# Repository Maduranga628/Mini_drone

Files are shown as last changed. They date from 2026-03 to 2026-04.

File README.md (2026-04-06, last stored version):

## ESP-Drone

* [中文](./README_cn.md)

### Introduction

**ESP-Drone** is an open source solution based on Espressif ESP32/ESP32-S2/ESP32-S3 Wi-Fi chip, which can be controlled by a mobile APP or gamepad over **Wi-Fi** connection. ESP-Drone comes with **simple hardware**, **clear and extensible code architecture**, and therefore this project can be used in **STEAM education** and other fields. The main code is ported from **Crazyflie** open source project with **GPL3.0** protocol.

> Currently support ESP32、ESP32S2、ESP32S3, please using ESP-IDF [release/v4.4](https://docs.espressif.com/projects/esp-idf/en/release-v4.4/esp32s2/get-started/index.html) branch as your develop environment

ESP-Drone

For more information, please check the sections below:
* **Getting Started**: [Getting Started](https://docs.espressif.com/projects/espressif-esp-drone/zh_CN/latest/gettingstarted.html)
* **Hardware Schematic**：[Hardware](https://docs.espressif.com/projects/espressif-esp-drone/zh_CN/latest/_static/ESP32_S2_Drone_V1_2/SCH_Mainboard_ESP32_S2_Drone_V1_2.pdf)
* **iOS APP Source code**: [ESP-Drone-iOS](https://github.com/EspressifApps/ESP-Drone-iOS)
* **Android APP Source code**: [ESP-Drone-Android](https://github.com/EspressifApps/ESP-Drone-Android)

### Features

1. Stabilize Mode
2. Height-hold Mode
3. Position-hold Mode
4. APP Control
5. CFclient Supported

Note: to implement Height-hold/Position-hold mode, extension boards are needed. For more information, see Hardware Reference. 

### Third Party Copyrighted Code

Additional third party copyrighted code is included under the following licenses.

| Component | License | Origin |Commit ID |
| :---:  | :---: | :---: |:---: |
| core/crazyflie | GPL3.0  |[Crazyflie](https://github.com/bitcraze/crazyflie-firmware) |tag_2021_01 b448553|
| lib/dsp_lib |  | [esp32-lin](https://github.com/whyengineer/esp32-lin/tree/master/components/dsp_lib) |6fa39f4c|

### Support Policy

From December 2022, we will offer limited support on this project, but Pull Request is still welcomed!

### THANKS

1. Thanks to Bitcraze for the great [Crazyflie project](https://www.bitcraze.io/%20).
2. Thanks to Espressif for the powerful [ESP-IDF framework](https://docs.espressif.com/projects/esp-idf/en/latest/esp32s2/get-started/index.html).
3. Thanks to WhyEngineer for the useful [ESP-DSP lib](https://github.com/whyengineer/esp32-lin/tree/master/components/dsp_lib).

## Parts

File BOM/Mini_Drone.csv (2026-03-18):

Reference | Qty | Value | DNP | Exclude from BOM | Exclude from Board | Footprint | Datasheet | LCSC No. | LCSC No. | MANUFACTURER | Manufacturer | Manufacturer Part No. | Manufacturer Part No.
C1,C2,C3,C4,C5,C6,C7,C8,C9,C10,C11,C12,C13,C14,C22,C23 | 16 | 1u |  |  |  | Capacitor_SMD:C_0603_1608Metric | ~ |  | C106214 |  | YAGEO |  | CC0603KRX5R6BB105
C15,C16,C18,C19,C20,C21 | 6 | 100n |  |  |  | Capacitor_SMD:C_0603_1608Metric | ~ |  | C14663 |  | YAGEO |  | CC0603KRX7R9BB104
C17 | 1 | 15p |  |  |  | Capacitor_SMD:C_0402_1005Metric | ~ |  | C106997 |  | YAGEO |  | CC0402JRNPO9BN150
D1,D2,D3,D4 | 4 | 1N4148W |  |  |  | Diode_SMD:D_SOD-123 | https://www.vishay.com/docs/85748/1n4148w.pdf | C917030 |  |  | JSMSEMI |  | 1N4148W
D5 | 1 | SS24 |  |  |  | Diode_SMD:D_SMA | https://www.vishay.com/docs/88748/ss22.pdf | C908678 |  |  | GOODWORK |  | SS24
D6,D9,D10 | 3 | LED | DNP |  | Excluded from board | LED_SMD:LED_0603_1608Metric | ~ |  | C965804 |  | XINGLIGHT |  | XL-1608UGC-04
D7,D8,D11 | 3 | LED |  |  |  | LED_SMD:LED_0603_1608Metric | ~ |  | C965804 |  | XINGLIGHT |  | XL-1608UGC-04
H1,H2,H3,H4 | 4 | MountingHole_Pad | DNP | Excluded from BOM | Excluded from board | MountingHole:MountingHole_2.2mm_M2_Pad_Via | ~
H5,H6,H7 | 3 | MountingHole |  | Excluded from BOM |  | MountingHole:MountingHole_2.2mm_M2 | ~
H8 | 1 | MountingHole | DNP | Excluded from BOM | Excluded from board | MountingHole:MountingHole_2.2mm_M2 | ~
J1,J2,J3,J4 | 4 | JST_02_Pin | DNP | Excluded from BOM | Excluded from board | Connector_PinHeader_2.54mm:PinHeader_1x02_P2.54mm_Vertical | ~
J5 | 1 | Conn_01x08_Pin |  |  |  | Connector_PinSocket_2.54mm:PinSocket_1x08_P2.54mm_Vertical | ~
JP1 | 1 | Jumper_2_Small_Open |  | Excluded from BOM |  | Jumper:SolderJumper-2_P1.3mm_Open_RoundedPad1.0x1.5mm | ~
J_BAT1 | 1 | BAT_Conn |  | Excluded from BOM |  | Connector_PinHeader_2.54mm:PinHeader_1x02_P2.54mm_Vertical | ~
J_CAM1 | 1 | FPC_Conn_01x24_Pin |  |  |  | Mini_Drone:TE_2-1734839-4_1x24-1MP_P0.5mm_Horizontal | ~ | C2856805 |  |  | XUNPU |  | FPC-05F-24PH20
J_USB1 | 1 | USB_C |  |  |  | Connector_USB:USB_C_Receptacle_GCT_USB4105-xx-A_16P_TopMnt_Horizontal | https://www.usb.org/sites/default/files/documents/usb_type-c.zip | C2988369 |  |  | G-Switch |  | GT-USB-7010ASV
Q1,Q2,Q3,Q4 | 4 | AO3400A |  |  |  | Package_TO_SOT_SMD:SOT-23 | http://www.aosmd.com/pdfs/datasheet/AO3400A.pdf | C347475 |  |  | UMW |  | AO3400A
Q5 | 1 | AO3401A |  |  |  | Package_TO_SOT_SMD:SOT-23 | http://www.aosmd.com/pdfs/datasheet/AO3401A.pdf | C347476 |  |  | UMW |  | AO3401A
R1,R2,R3,R4,R16,R17,R18,R20,R21,R22 | 10 | 10k |  |  |  | Resistor_SMD:R_0603_1608Metric | ~ | C99198 |  |  | YAGEO |  | RC0603JR-0710KL
R5 | 1 | 100k |  |  |  | Resistor_SMD:R_0603_1608Metric | ~ | C100048 |  |  | YAGEO |  | RC0603JR-07100KL
R6 | 1 | 220k |  |  |  | Resistor_SMD:R_0603_1608Metric | ~ | C137647 |  |  | YAGEO |  | RC0603JR-07220KL
R7,R8 | 2 | 5k1 |  |  |  | Resistor_SMD:R_0603_1608Metric | ~ | C14677 |  |  | YAGEO |  | RC0603JR-075K1L
R9 | 1 | 1k | DNP |  | Excluded from board | Resistor_SMD:R_0603_1608Metric | ~ | C14676 |  |  | YAGEO |  | RC0603JR-071KL
R10,R12,R19 | 3 | 1k |  |  |  | Resistor_SMD:R_0603_1608Metric | ~ | C14676 |  |  | YAGEO |  | RC0603JR-071KL
R11 | 1 | 3k3 |  |  |  | Resistor_SMD:R_0603_1608Metric | ~ | C114432 |  |  | YAGEO |  | RC0603JR-073K3L
R13,R14 | 2 | 330R | DNP |  | Excluded from board | Resistor_SMD:R_0603_1608Metric | ~ | C105879 |  |  | YAGEO |  | RC0603JR-07330RL
R15 | 1 | 330R |  |  |  | Resistor_SMD:R_0603_1608Metric | ~ | C105879 |  |  | YAGEO |  | RC0603JR-07330RL
U1 | 1 | TP4057 |  |  |  | Package_TO_SOT_SMD:TSOT-23-6 | http://toppwr.com/uploadfile/file/20230304/640302a47b738.pdf | C7473159 |  |  | MSKSEMI |  | TP4057-MS
U2 | 1 | TLV75733PDBV |  |  |  | Package_TO_SOT_SMD:SOT-23-5 | https://www.ti.com/lit/ds/symlink/tlv757p.pdf | C485517 |  |  | Texas Instruments |  | TLV75733PDBVR
U3 | 1 | SSP7615-12MR |  |  |  | Package_TO_SOT_SMD:SOT-23-3 | https://www.lcsc.com/datasheet/C7545816.pdf | C7545816 |  |  | Siproin |  | SSP7615-12MR
U4 | 1 | SSP6206-28MR |  |  |  | Package_TO_SOT_SMD:SOT-23-3 | https://www.lcsc.com/datasheet/C2845046.pdf | C2845046 |  |  | Siproin |  | SSP6206-28MR
U5 | 1 | BMI270 |  |  |  | Mini_Drone:BMI270 | https://www.lcsc.com/datasheet/C2836813.pdf | C2836813 |  | Bosch Sensortec | Bosch Sensortec |  | BMI270
U6 | 1 | ESP32-S3-MINI-1-N8 |  |  |  | Mini_Drone:ESP32-S3-MINI-1 | https://www.lcsc.com/datasheet/C3013941.pdf | C3013941 |  |  | Espressif | ESP32-S3-MINI-1-N4R2

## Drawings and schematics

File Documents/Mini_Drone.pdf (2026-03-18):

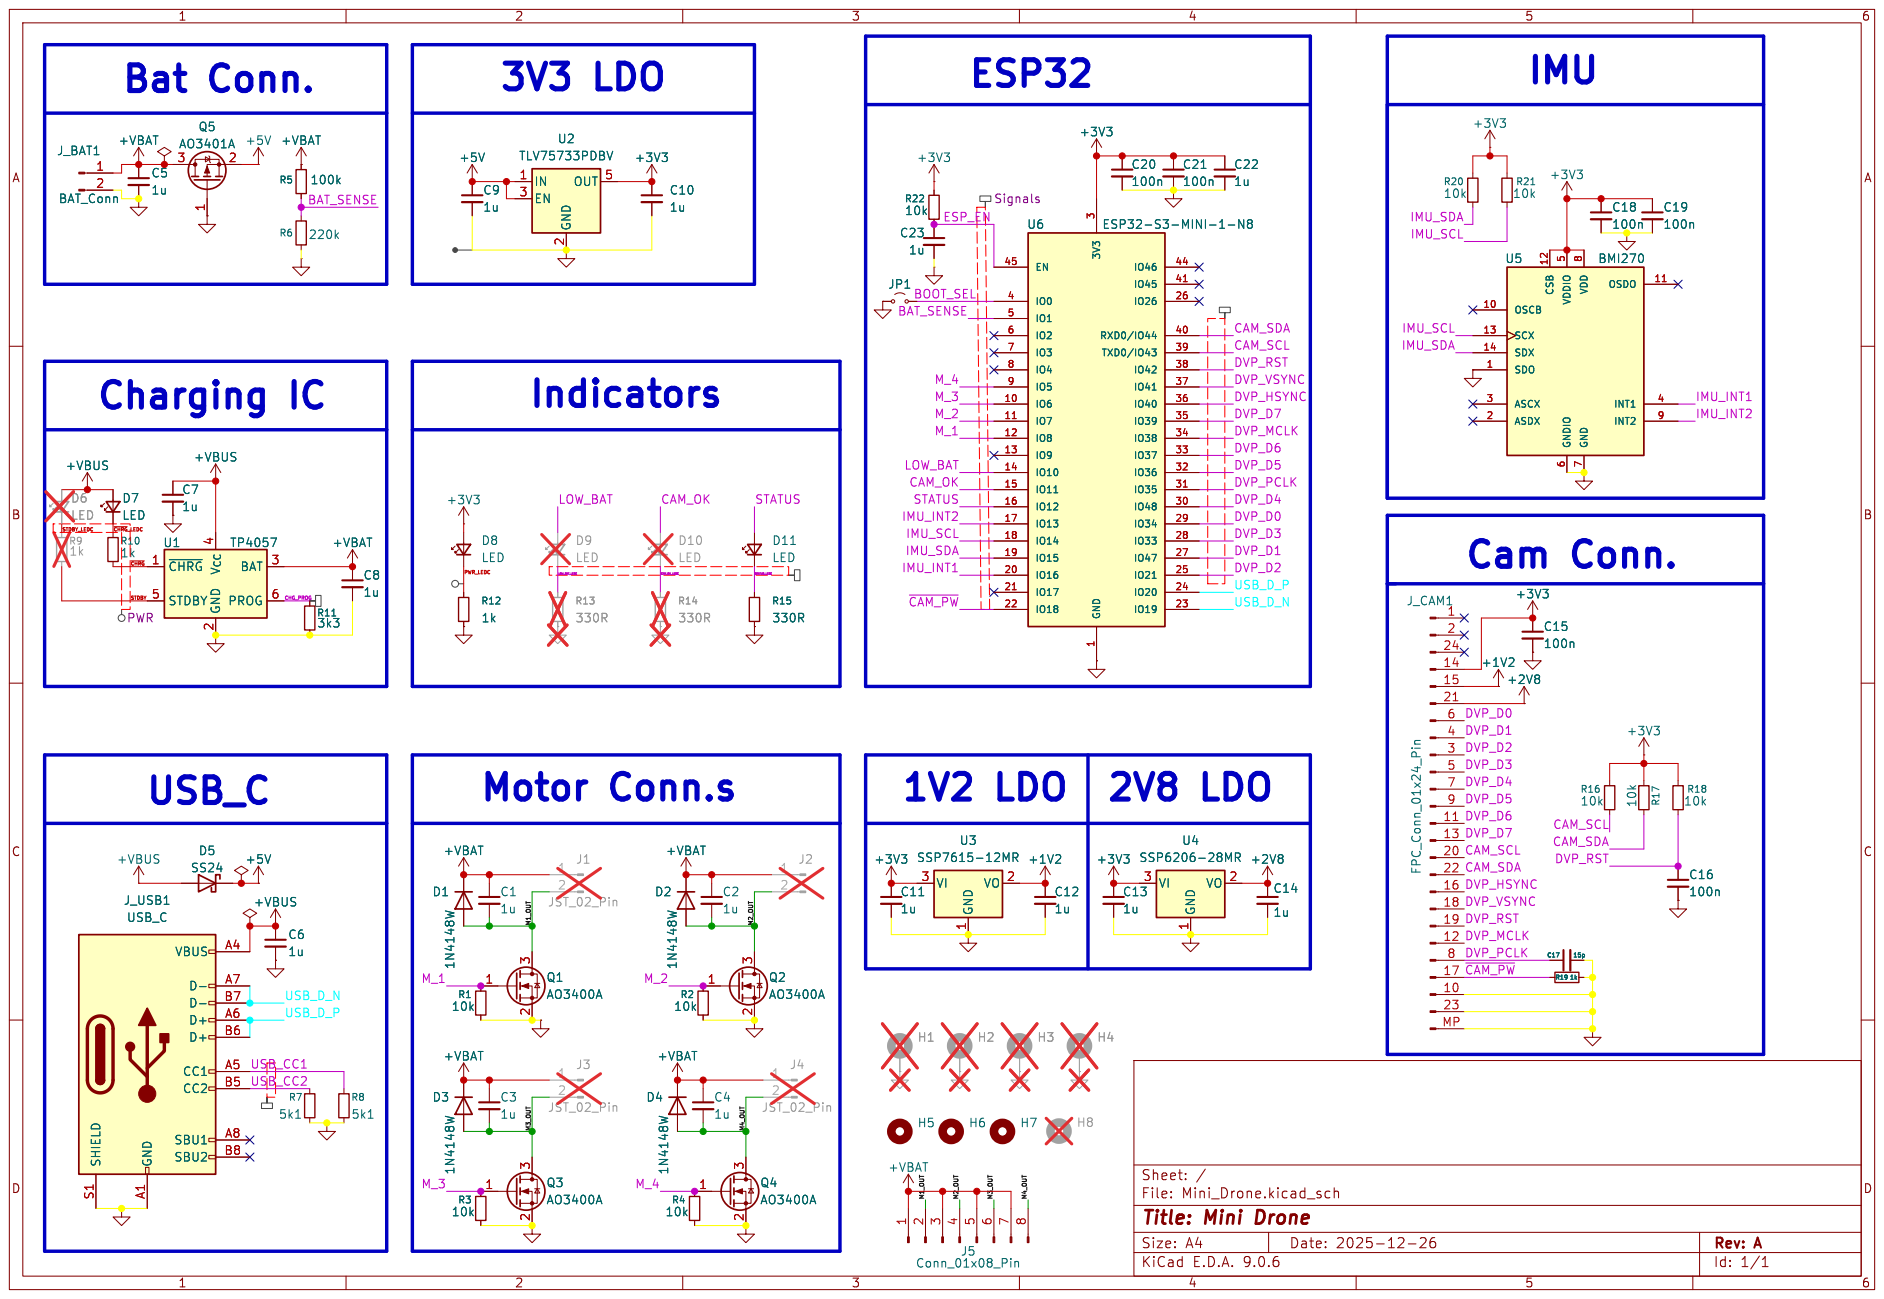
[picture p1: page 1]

Id: 1/1 Title: Mini Drone

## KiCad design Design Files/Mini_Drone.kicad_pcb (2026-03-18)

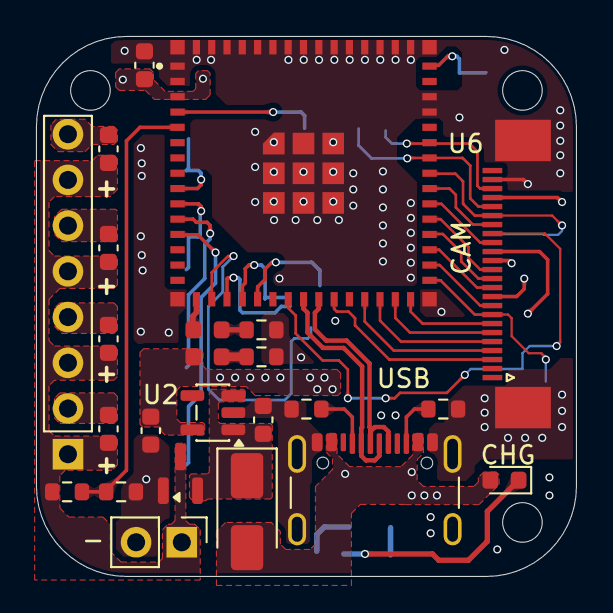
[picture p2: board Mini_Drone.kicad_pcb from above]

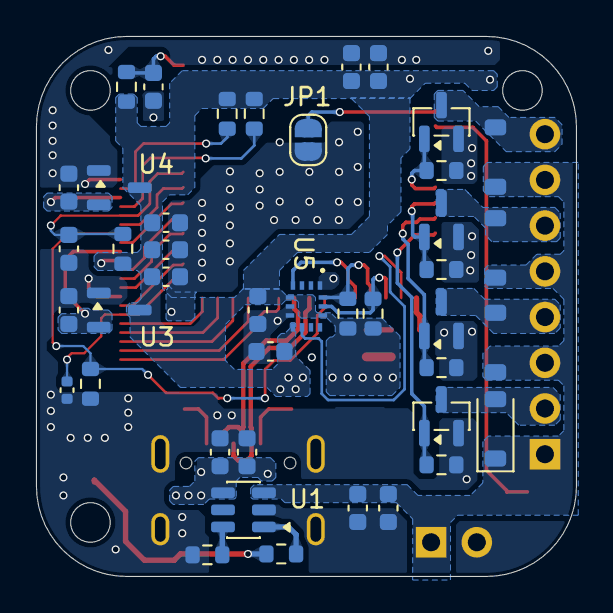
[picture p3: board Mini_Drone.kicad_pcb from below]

Board: 4 copper layers, 30.0 x 30.0 mm, 69 parts (42 on the bottom side), 48 nets.

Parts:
-: BAT_Conn; PinHeader_1x02_P2.54mm_Vertical
C1, C2, C3, C4, C5, C6, C7, C8, C9, C10, C11, C12, C13, C14, C22, C23: 1u; C_0603_1608Metric
C15, C16, C18, C19, C20, C21: 100n; C_0603_1608Metric
C17: 15p; C_0402_1005Metric
CAM: FPC_Conn_01x24_Pin; TE_2-1734839-4_1x24-1MP_P0.5mm_Horizontal
CHG: LED; LED_0603_1608Metric
D1, D2, D3, D4: 1N4148W; D_SOD-123
D5: SS24; D_SMA
D8, D11: LED; LED_0603_1608Metric
H5, H6, H7: MountingHole; MountingHole_2.2mm_M2
J5: Conn_01x08_Pin; PinSocket_1x08_P2.54mm_Vertical
JP1: Jumper_2_Small_Open; SolderJumper-2_P1.3mm_Open_RoundedPad1.0x1.5mm
Q1, Q2, Q3, Q4: AO3400A; SOT-23
Q5: AO3401A; SOT-23
R1, R2, R3, R4, R16, R17, R18, R20, R21, R22: 10k; R_0603_1608Metric
R5: 100k; R_0603_1608Metric
R6: 220k; R_0603_1608Metric
R7, R8: 5k1; R_0603_1608Metric
R10, R12, R19: 1k; R_0603_1608Metric
R11: 3k3; R_0603_1608Metric
R15: 330R; R_0603_1608Metric
U1: TP4057; TSOT-23-6
U2: TLV75733PDBV; SOT-23-5
U3: SSP7615-12MR; SOT-23-3
U4: SSP6206-28MR; SOT-23-3
U5: BMI270
U6: ESP32-S3-MINI-1-N8; ESP32-S3-MINI-1
USB: USB_C; USB_C_Receptacle_GCT_USB4105-xx-A_16P_TopMnt_Horizontal

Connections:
+1V2: C12.1, CAM.15, U3.2 (VO)
+2V8: C14.1, CAM.21, U4.2 (VO)
+3V3: C10.1, C11.1, C13.1, C15.1, C18.1, C19.1, C20.1, C21.1, C22.1, CAM.14, D8.2 (A), R16.1, R17.1, R18.1, R20.1, R21.1, R22.1, U2.5 (OUT), U3.3 (VI), U4.3 (VI), U5.5 (VDDIO), U5.8 (VDD), U5.12 (CSB), U6.3 (3V3)
+5V: C9.1, D5.1 (K), Q5.2 (S), U2.1 (IN), U2.3 (EN)
+VBAT: -.1, C1.1, C2.1, C3.1, C4.1, C5.1, C8.1, D1.1 (K), D2.1 (K), D3.1 (K), D4.1 (K), J5.1, J5.3, J5.5, J5.7, Q5.3 (D), R5.1, U1.3 (BAT)
+VBUS: C6.1, C7.1, CHG.2 (A), D5.2 (A), U1.4 (V_{CC}), USB.A4 (VBUS), USB.A9 (VBUS), USB.B4 (VBUS), USB.B9 (VBUS)
/BAT_SENSE: R5.2, R6.1, U6.5 (IO1)
/BOOT_SEL: JP1.2 (B), U6.4 (IO0)
/CAM_SCL: CAM.20, R16.2, U6.39 (TXD0/IO43)
/CAM_SDA: CAM.22, R17.2, U6.40 (RXD0/IO44)
/CHG_PROG: R11.1, U1.6 (PROG)
/DVP_D0: CAM.6, U6.29 (IO34)
/DVP_D1: CAM.4, U6.27 (IO47)
/DVP_D2: CAM.3, U6.25 (IO21)
/DVP_D3: CAM.5, U6.28 (IO33)
/DVP_D4: CAM.7, U6.30 (IO48)
/DVP_D5: CAM.9, U6.32 (IO36)
/DVP_D6: CAM.11, U6.33 (IO37)
/DVP_D7: CAM.13, U6.35 (IO39)
/DVP_HSYNC: CAM.16, U6.36 (IO40)
/DVP_MCLK: CAM.12, U6.34 (IO38)
/DVP_PCLK: C17.1, CAM.8, U6.31 (IO35)
/DVP_RST: C16.1, CAM.19, R18.2, U6.38 (IO42)
/DVP_VSYNC: CAM.18, U6.37 (IO41)
/ESP_EN: C23.1, R22.2, U6.45 (EN)
/IMU_INT1: U5.4 (INT1), U6.20 (IO16)
/IMU_INT2: U5.9 (INT2), U6.17 (IO13)
/IMU_SCL: R21.2, U5.13 (SCX), U6.18 (IO14)
/IMU_SDA: R20.2, U5.14 (SDX), U6.19 (IO15)
/M1_OUT: C1.2, D1.2 (A), J5.2, Q1.3 (D)
/M2_OUT: C2.2, D2.2 (A), J5.4, Q2.3 (D)
/M3_OUT: C3.2, D3.2 (A), J5.6, Q3.3 (D)
/M4_OUT: C4.2, D4.2 (A), J5.8, Q4.3 (D)
/M_1: Q1.1 (G), R1.1, U6.12 (IO8)
/M_2: Q2.1 (G), R2.1, U6.11 (IO7)
/M_3: Q3.1 (G), R3.1, U6.10 (IO6)
/M_4: Q4.1 (G), R4.1, U6.9 (IO5)
/PWR_LEDC: D8.1 (K), R12.1
/STATUS: D11.2 (A), U6.16 (IO12)
/STATUS_LEDC: D11.1 (K), R15.1
/USB_CC1: R8.1, USB.A5 (CC1)
/USB_CC2: R7.1, USB.B5 (CC2)
/USB_D_N: U6.23 (IO19), USB.A7 (D-), USB.B7 (D-)
/USB_D_P: U6.24 (IO20), USB.A6 (D+), USB.B6 (D+)
/~CAM_PW: CAM.17, R19.1, U6.22 (IO18)
/~CHRG: R10.2, U1.1 (~CHRG)
/~CHRG_LEDC: CHG.1 (K), R10.1
GND: -.2, C5.2, C6.2, C7.2, C8.2, C9.2, C10.2, C11.2, C12.2, C13.2, C14.2, C15.2, C16.2, C17.2, C18.2, C19.2, C20.2, C21.2, C22.2, C23.2, CAM.10, CAM.23, CAM.MP (Pad), JP1.1 (A), Q1.2 (S), Q2.2 (S), Q3.2 (S), Q4.2 (S), Q5.1 (G), R1.2, R2.2, R3.2, R4.2, R6.2, R7.2, R8.2, R11.2, R12.2, R15.2, R19.2, U1.2 (GND), U2.2 (GND), U3.1 (GND), U4.1 (GND), U5.1 (SDO), U5.6 (GNDIO), U5.7 (GND), U6.1 (GND), U6.2 (GND__1), U6.42 (GND__2), U6.43 (GND__3), U6.46 (GND__4), U6.47 (GND__5), U6.48 (GND__6), U6.49 (GND__7), U6.50 (GND__8), U6.51 (GND__9), U6.52 (GND__10), U6.53 (GND__11), U6.54 (GND__12), U6.55 (GND__13), U6.56 (GND__14), U6.57 (GND__15), U6.58 (GND__16), U6.59 (GND__17), U6.60 (GND__18), U6.61 (GND__19), U6.61_1 (GND__20), U6.61_2 (GND__21), U6.61_3 (GND__22), U6.61_4 (GND__23), U6.61_5 (GND__24), U6.61_6 (GND__25), U6.61_7 (GND__26), U6.61_8 (GND__27), U6.62 (GND__28), U6.63 (GND__29), U6.64 (GND__30), U6.65 (GND__31), USB.A1 (GND), USB.A12 (GND), USB.B1 (GND), USB.B12 (GND), USB.S1 (SHIELD)

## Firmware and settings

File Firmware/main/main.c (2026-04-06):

/*
 * ESP-Drone Firmware
 * 
 * Copyright 2019-2020  Espressif Systems (Shanghai) 
 * Copyright (C) 2011-2012 Bitcraze AB
 *
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
 */

#include <stdint.h>
#include <stdio.h>
#include <stdlib.h>

#include "freertos/FreeRTOS.h"
#include "freertos/task.h"
#include "freertos/portmacro.h"
#include "nvs_flash.h"

#include "stm32_legacy.h"
#include "platform.h"
#include "system.h"
#define DEBUG_MODULE "APP_MAIN"
#include "debug_cf.h"

void app_main()
{
    /*
    * Initialize the platform and Launch the system task
    * app_main will initialize and start everything
    */

    /* initialize nvs flash prepare for Wi-Fi */
    esp_err_t ret = nvs_flash_init();

    if (ret == ESP_ERR_NVS_NO_FREE_PAGES || ret == ESP_ERR_NVS_NEW_VERSION_FOUND) {
        ESP_ERROR_CHECK(nvs_flash_erase());
        ret = nvs_flash_init();
    }

    ESP_ERROR_CHECK(ret);

    /*Initialize the platform.*/
    if (platformInit() == false) {
        while (1);//if  firmware is running on the wrong hardware, Halt
    }

    /*launch the system task */
    systemLaunch();

}

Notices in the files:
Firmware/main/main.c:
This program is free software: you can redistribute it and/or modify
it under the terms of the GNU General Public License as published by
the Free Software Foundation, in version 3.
